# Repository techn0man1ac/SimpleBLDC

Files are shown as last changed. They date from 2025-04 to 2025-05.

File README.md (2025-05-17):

# SimpleBLDC

This is simple Arduino based 650W BLDC motor(with Hall sensors) controller. Designed with [KiCAD](https://www.kicad.org/). This controller has version V0.1, which means it is still under development. **The source files can be changed.**

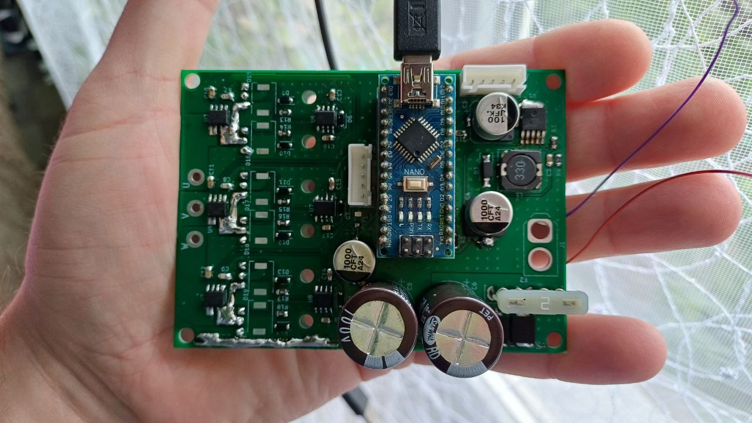
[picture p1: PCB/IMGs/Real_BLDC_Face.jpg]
SimpleBLDC PCB in real life


Simple BLDC 3-Phase BLDC motor driver specs:
- Battery: 8S 
- VCC: 24.0V to 33.6V
- I(max): 20A 
- Сurrent measurements per phase

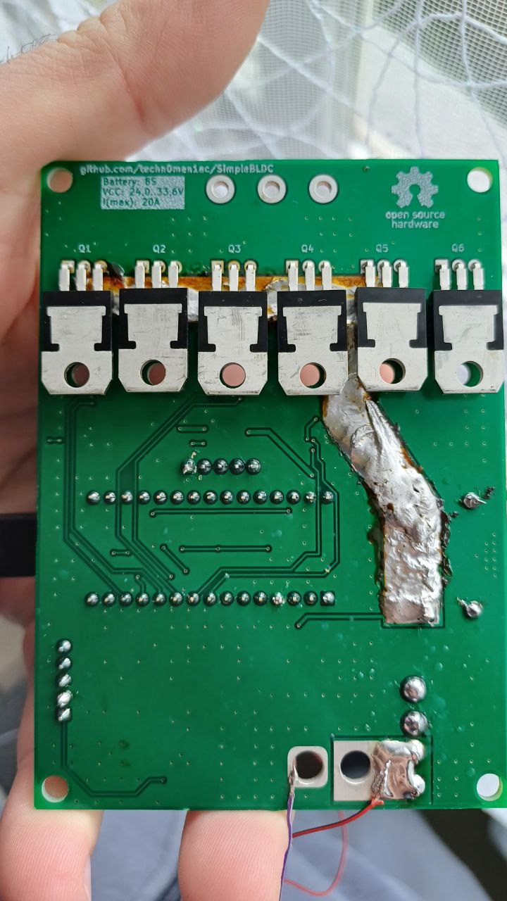
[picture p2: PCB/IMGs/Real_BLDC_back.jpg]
SimpleBLDC PCB in real life_back


The device has the following features:
- XT60 power connector;
- Arduino Nano V3.0 main controller;
- Overcurrent protection (fuse);
- Reverse polarity protection;
- The ability to work with non-collector motors via Hall sensors (electric scooter or electric bicycle);
- Monitoring and control of the current of each phase (current is measured in both positive and negative directions);
- Current control by PWM, operating frequency 16/32 kHz;
- Has a connector for connecting a traction control potentiometer and a reverse button.
- Publication of the project under the [MIT license](https://github.com/techn0man1ac/SimpleBLDC/blob/main/LICENSE).

# Schematic

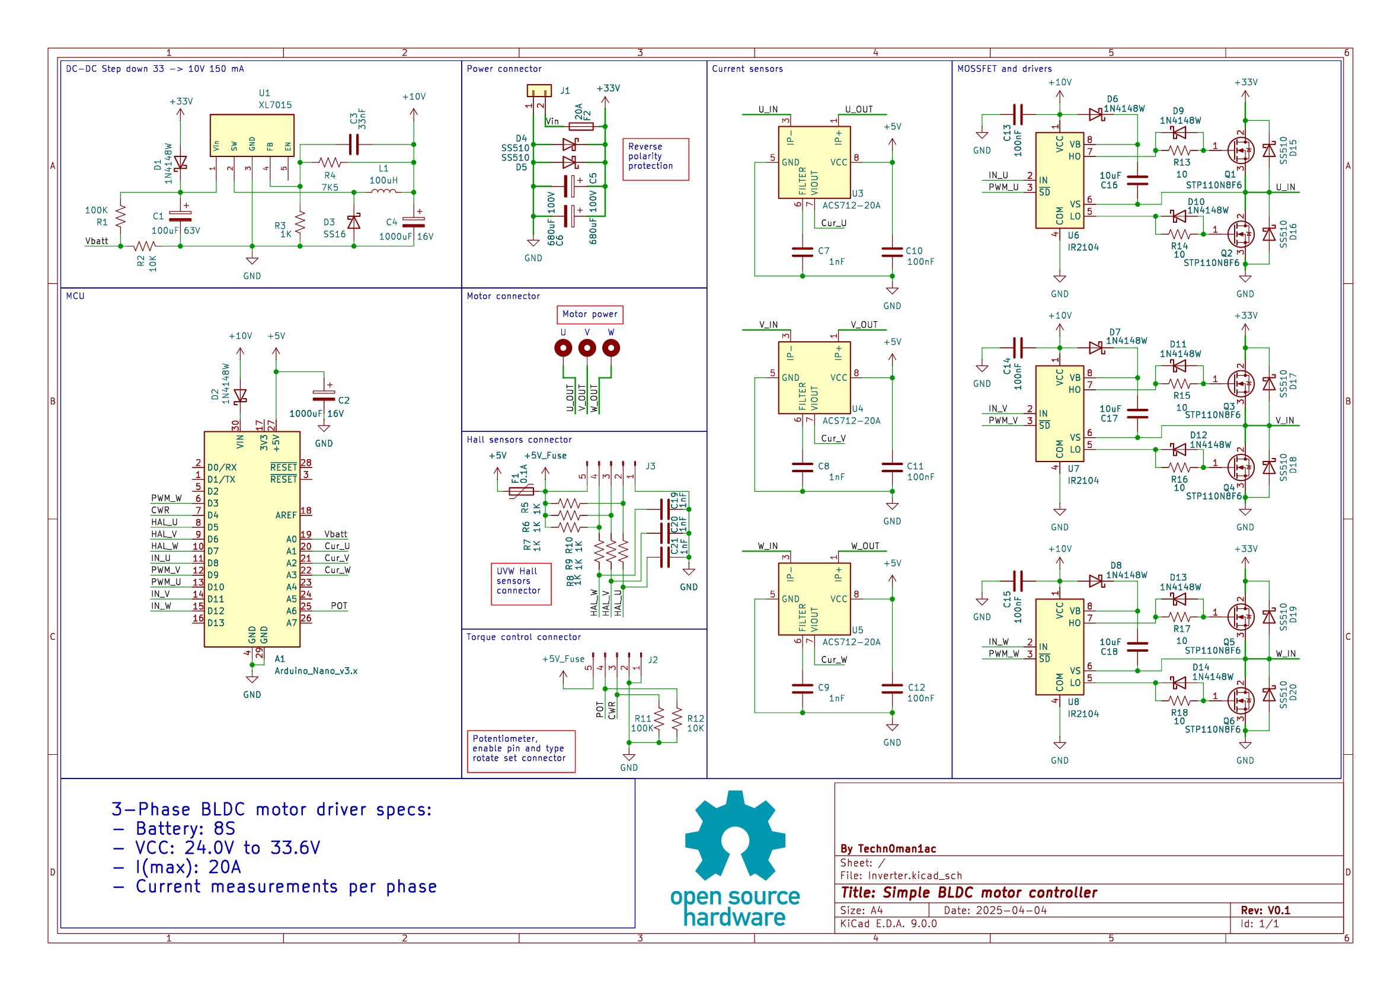
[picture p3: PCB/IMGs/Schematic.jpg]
BLDC motor driver schematic


The device has 3 drivers for mosfet transistors, as well as 3 current sensors based on the Hall effect, which measure both in the positive and negative directions. The use of 3 sensors is the reason for the development of the device for regenerative braking.

# PCB

The board consists of two layers: top and bottom. All the main parts are located on the top layer.

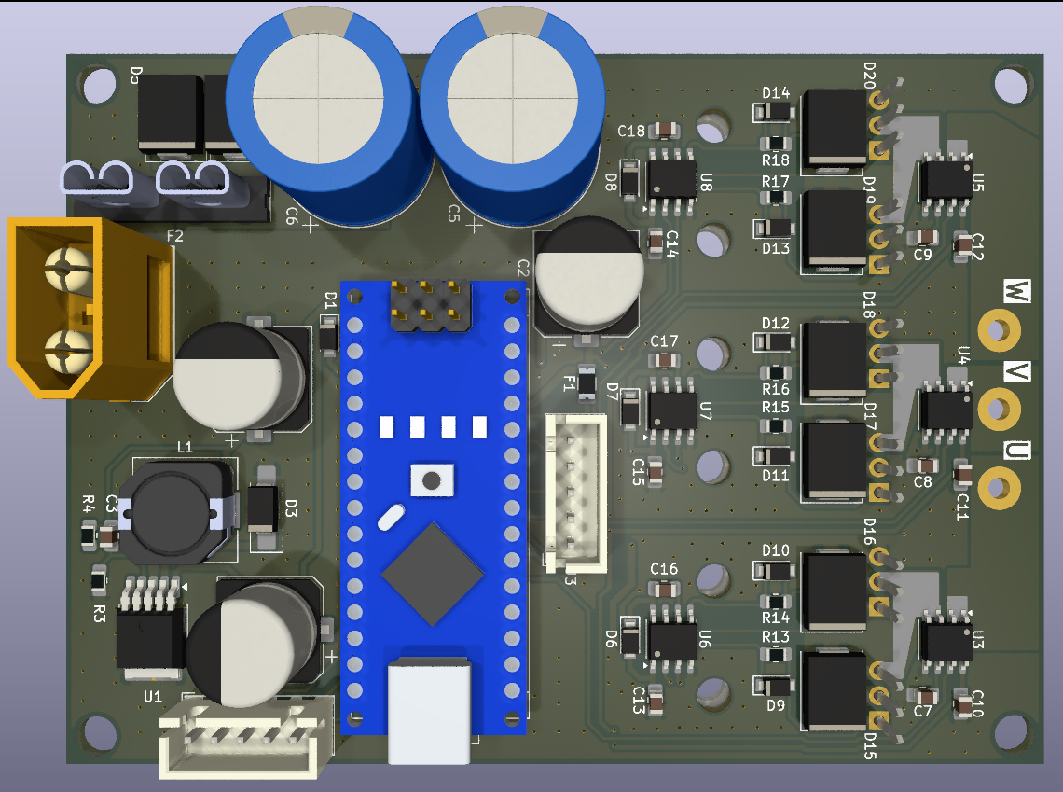
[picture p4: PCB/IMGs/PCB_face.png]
Face PCB side


The bottom layer contains mainly earth and power tracks.

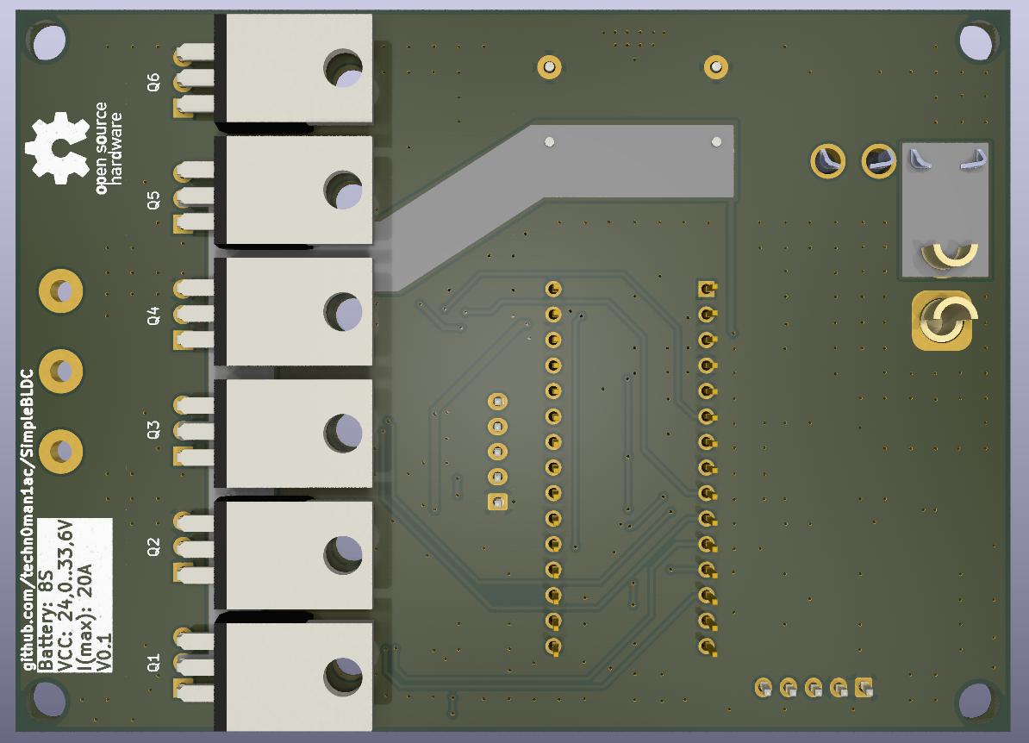
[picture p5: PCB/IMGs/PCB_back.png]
The PCB bottom laye


Board sizes is 72 x 99 mm:

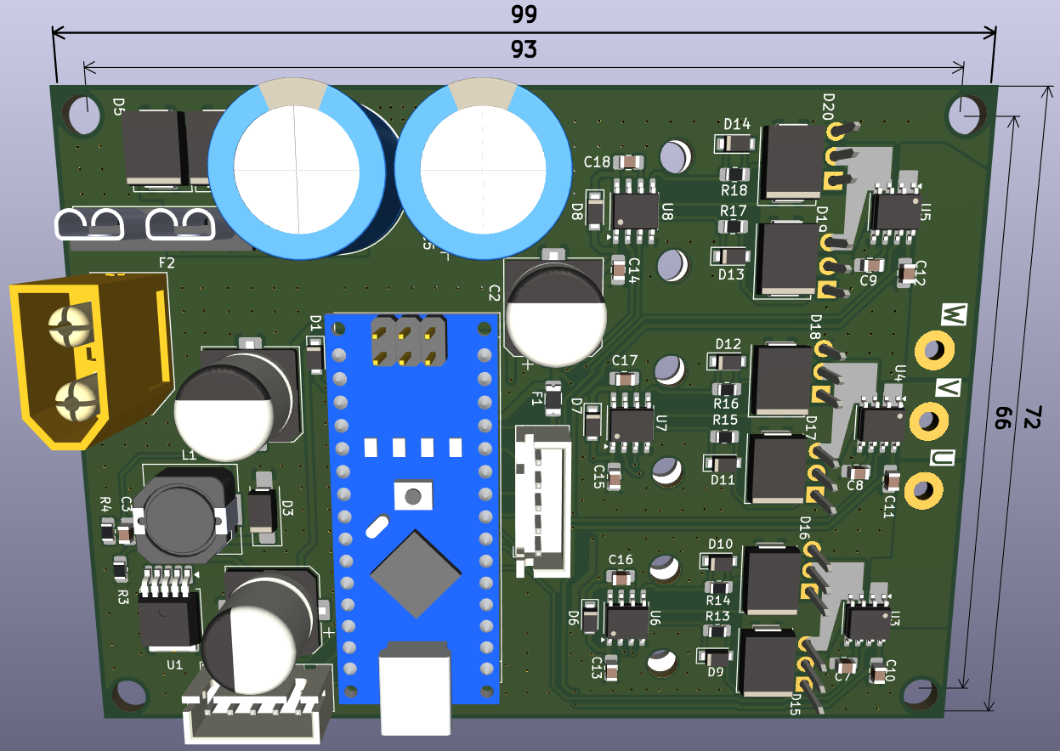
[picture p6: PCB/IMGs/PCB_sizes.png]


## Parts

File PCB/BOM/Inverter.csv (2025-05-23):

Reference | Qty | Value | DNP | Exclude from BOM | Exclude from Board | Footprint | Datasheet | Опис
A1 | 1 | Arduino_Nano_v3.x |  | Excluded from BOM |  | Module:Arduino_Nano | http://www.mouser.com/pdfdocs/Gravitech_Arduino_Nano3_0.pdf | Arduino Nano v3.x
C1 | 1 | 100uF 63V |  |  |  | Capacitor_SMD:CP_Elec_10x10.5 | ~ | Polarized capacitor
C2,C4 | 2 | 1000uF 16V |  |  |  | Capacitor_SMD:CP_Elec_10x10.5 | ~ | Polarized capacitor
C3 | 1 | 33nF |  |  |  | Capacitor_SMD:C_0805_2012Metric_Pad1.18x1.45mm_HandSolder | ~ | Unpolarized capacitor
C5,C6 | 2 | 680uF 100V |  |  |  | Capacitor_THT:CP_Radial_D16.0mm_P7.50mm | ~ | 680uF 100V 105C
C7,C8,C9,C19,C20,C21 | 6 | 1nF |  |  |  | Capacitor_SMD:C_0805_2012Metric_Pad1.18x1.45mm_HandSolder | ~ | Unpolarized capacitor
C10,C11,C12,C13,C14,C15 | 6 | 100nF |  |  |  | Capacitor_SMD:C_0805_2012Metric_Pad1.18x1.45mm_HandSolder | ~ | Unpolarized capacitor
C16,C17,C18 | 3 | 10uF |  |  |  | Capacitor_SMD:C_0805_2012Metric_Pad1.18x1.45mm_HandSolder | ~ | Unpolarized capacitor
D1,D2,D6,D7,D8,D9,D10,D11,D12,D13,D14 | 11 | 1N4148W |  |  |  | Diode_SMD:Nexperia_CFP3_SOD-123W | https://www.vishay.com/docs/86356/1n4148w.pdf | 100V 150mA 4ns 150mA SOD-123 Switching Diode
D3 | 1 | SS16 |  |  |  | Diode_SMD:D_SMA_Handsoldering | https://www.vishay.com/docs/88746/ss12.pdf | 60V 1A Schottky Diode, SMA
D4,D5,D15,D16,D17,D18,D19,D20 | 8 | SS510 |  |  |  | Diode_SMD:ST_D_SMC | https://www.rectron.com/public/product_datasheets/ss510.pdf | Schottky diode SS510 5A 100V SMC
F1 | 1 | 0.1A |  |  |  | Fuse:Fuse_1206_3216Metric | ~ | 16V 500mA 1206 Resettable Fuse
F2 | 1 | 20A |  |  |  | Fuse:FUSE_3522-2 | ~ | ATO Blade Fuse Holder
J1 | 1 | Conn_01x02 |  |  |  | Connector_AMASS:AMASS_XT60-M_1x02_P7.20mm_Vertical | ~ | Generic connector, single row, 01x02, script generated (kicad-library-utils/schlib/autogen/connector/)
J2,J3 | 2 | Conn_01x05_Pin |  |  |  | Connector_JST:JST_XH_B5B-XH-A_1x05_P2.50mm_Vertical | ~ | Generic connector, single row, 01x05, script generated
L1 | 1 | 100uH |  |  |  | Inductor_SMD:L_10.4x10.4_H4.8 | ~ | Inductor
Q1,Q2,Q3,Q4,Q5,Q6 | 6 | STP110N8F6 |  |  |  | Package_TO_SOT_THT:TO-220-3_Horizontal_TabUp | https://www.st.com/resource/en/datasheet/stp110n8f6.pdf | N-channel 80 V, 0.0056 Ω typ.,110 A, STripFET™ F6 Power MOSFET in a TO-220 package
R1,R11 | 2 | 100K |  |  |  | Resistor_SMD:R_0805_2012Metric_Pad1.20x1.40mm_HandSolder | ~ | Resistor, US symbol
R2,R12 | 2 | 10K |  |  |  | Resistor_SMD:R_0805_2012Metric_Pad1.20x1.40mm_HandSolder | ~ | Resistor, US symbol
R3,R5,R6,R7,R8,R9,R10 | 7 | 1K |  |  |  | Resistor_SMD:R_0805_2012Metric_Pad1.20x1.40mm_HandSolder | ~ | Resistor, US symbol
R4 | 1 | 7K5 |  |  |  | Resistor_SMD:R_0805_2012Metric_Pad1.20x1.40mm_HandSolder | ~ | Resistor, US symbol
R13,R14,R15,R16,R17,R18 | 6 | 10 |  |  |  | Resistor_SMD:R_0805_2012Metric_Pad1.20x1.40mm_HandSolder | ~ | Resistor, US symbol
U1 | 1 | XL7015 |  |  |  | Package_TO_SOT_SMD:TO-252-5_TabPin3 | kicad-embed://datasheet-xl7015.pdf | Step-down type Adjustable 0.8A 5V~80V TO-252-5 DC-DC Converter
U2,V1,W1 | 3 | MountingHole_Pad |  | Excluded from BOM |  | MountingHole:MountingHole_2.2mm_M2_Pad | ~ | Mounting Hole with connection
U3,U4,U5 | 3 | ACS712-20A |  |  |  | Package_SO:SOIC-8_3.9x4.9mm_P1.27mm | http://www.allegromicro.com/~/media/Files/Datasheets/ACS712-Datasheet.ashx?la=en | ±20A Bidirectional Hall-Effect Current Sensor, +5.0V supply, 100mV/A, SOIC-8
U6,U7,U8 | 3 | IR2104 |  |  |  | Package_SO:SOIC-8_3.9x4.9mm_P1.27mm | https://www.infineon.com/dgdl/ir2104.pdf?fileId=5546d462533600a4015355c7c1c31671 | Half-Bridge Driver, 600V, 210/360mA, PDIP-8/SOIC-8

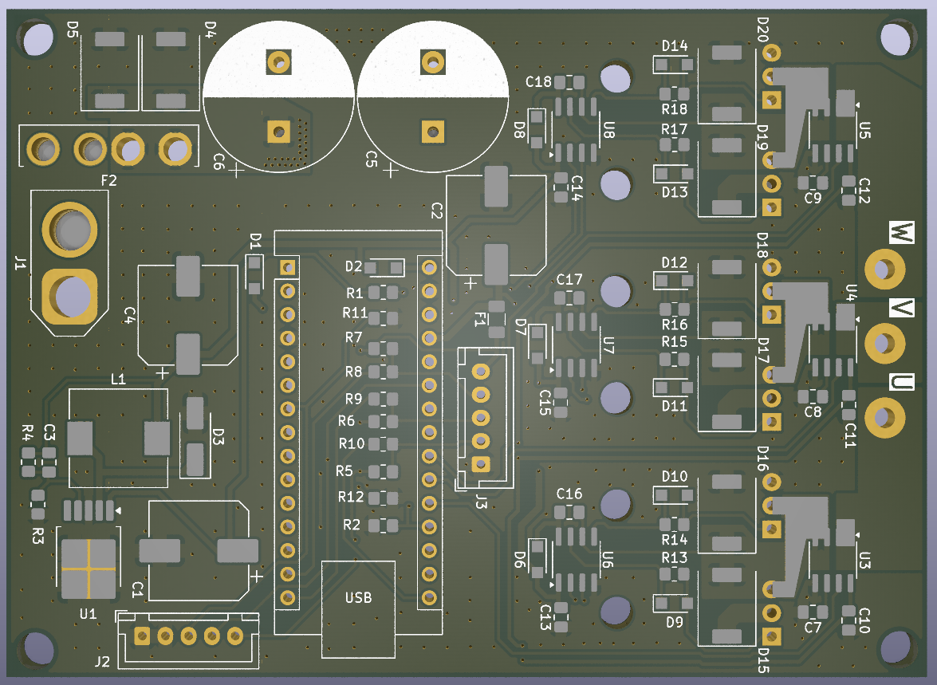
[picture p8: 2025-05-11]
PCB/IMGs/PCB_face_without_components.png

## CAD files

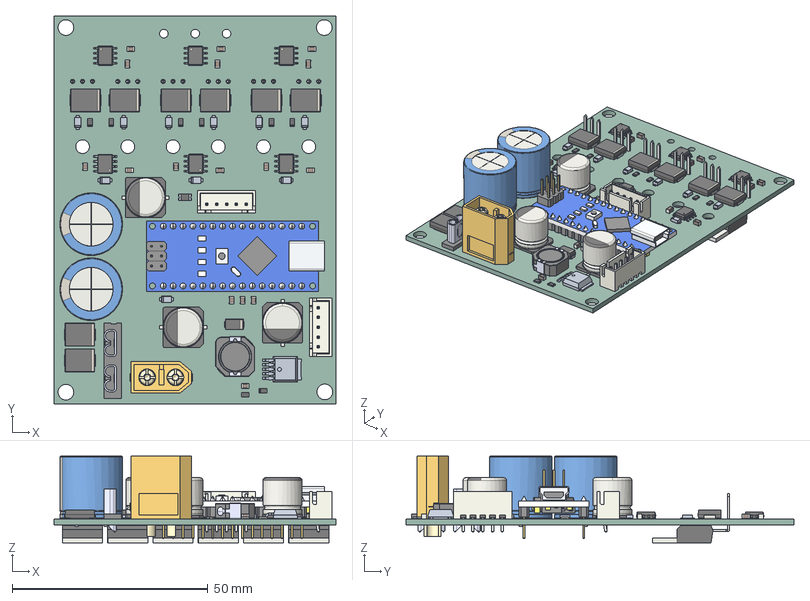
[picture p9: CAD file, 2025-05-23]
PCB/Board3D/Inverter.step
71.9 x 99.1 x 22.1 mm
JST_XH_B5B-XH-A_1x05_P2.50mm_Vertical x 2
D_SMC x 8
C_0805_2012Metric x 16
Inverter 1.5.1 x 11
R_0805_2012Metric x 18
SOIC-8_3.9x4.9mm_P1.27mm x 6
CP_Radial_D16.0mm_P7.50mm x 2
CDRH104RNP-150NC
CP_Elec_10x10.5 x 3
Arduino_Nano
Inverter 1.36.1
D_SMA
AMASS_XT60-M_1x02_P7.2mm_Vertical
solidIntersect
Terminal
TO-220-3_Horizontal_TabUp x 6
Inverter_PCB

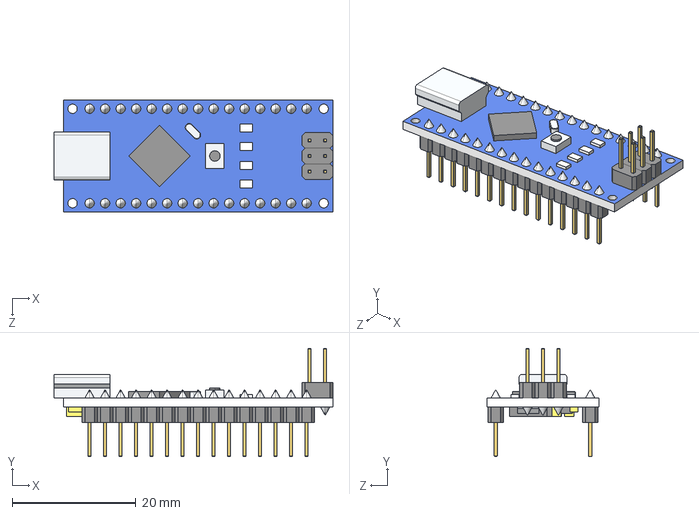
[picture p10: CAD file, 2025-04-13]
PCB/Components/Arduino/Arduino_Nano.STEP
45.0 x 17.5 x 18.0 mm

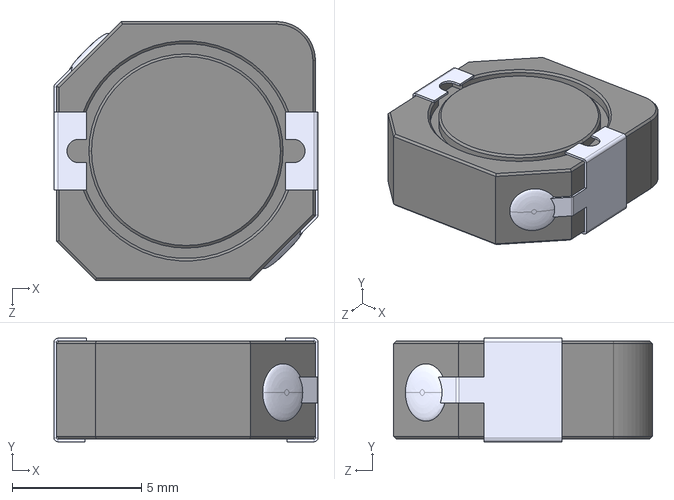
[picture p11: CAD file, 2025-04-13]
PCB/Components/CDRH104RNP/CDRH104RNP-150NC.STEP
10.2 x 4.00 x 10.0 mm

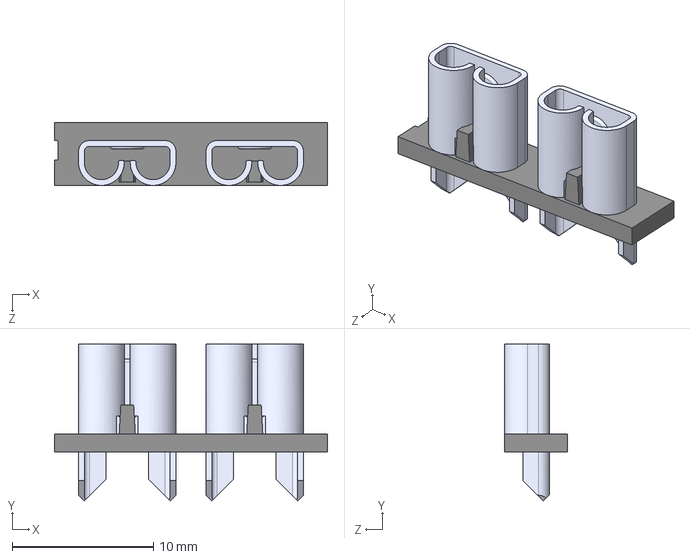
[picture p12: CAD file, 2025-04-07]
PCB/Components/Fuse Clips/3522-2--3DModel-STEP-56544.STEP
19.3 x 11.1 x 4.45 mm

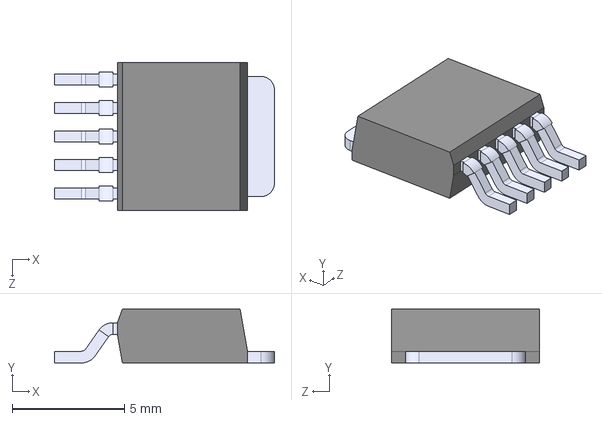
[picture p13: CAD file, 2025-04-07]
PCB/Components/XL7015/XL7015--3DModel-STEP-510211.STEP
9.80 x 2.40 x 6.60 mm

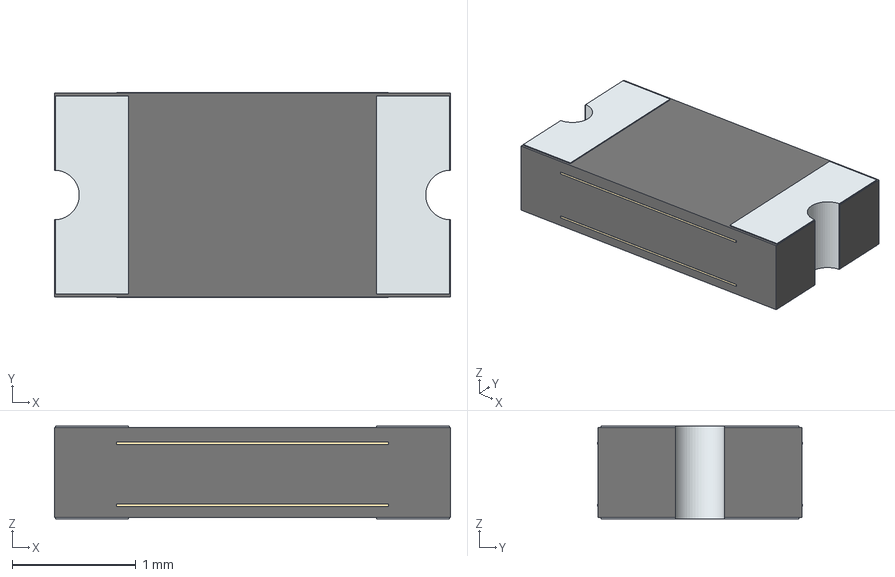
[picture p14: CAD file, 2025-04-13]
PCB/Components/PolyFuse/1206L035YR.stp
3.20 x 1.65 x 0.75 mm
solidIntersect
Terminal

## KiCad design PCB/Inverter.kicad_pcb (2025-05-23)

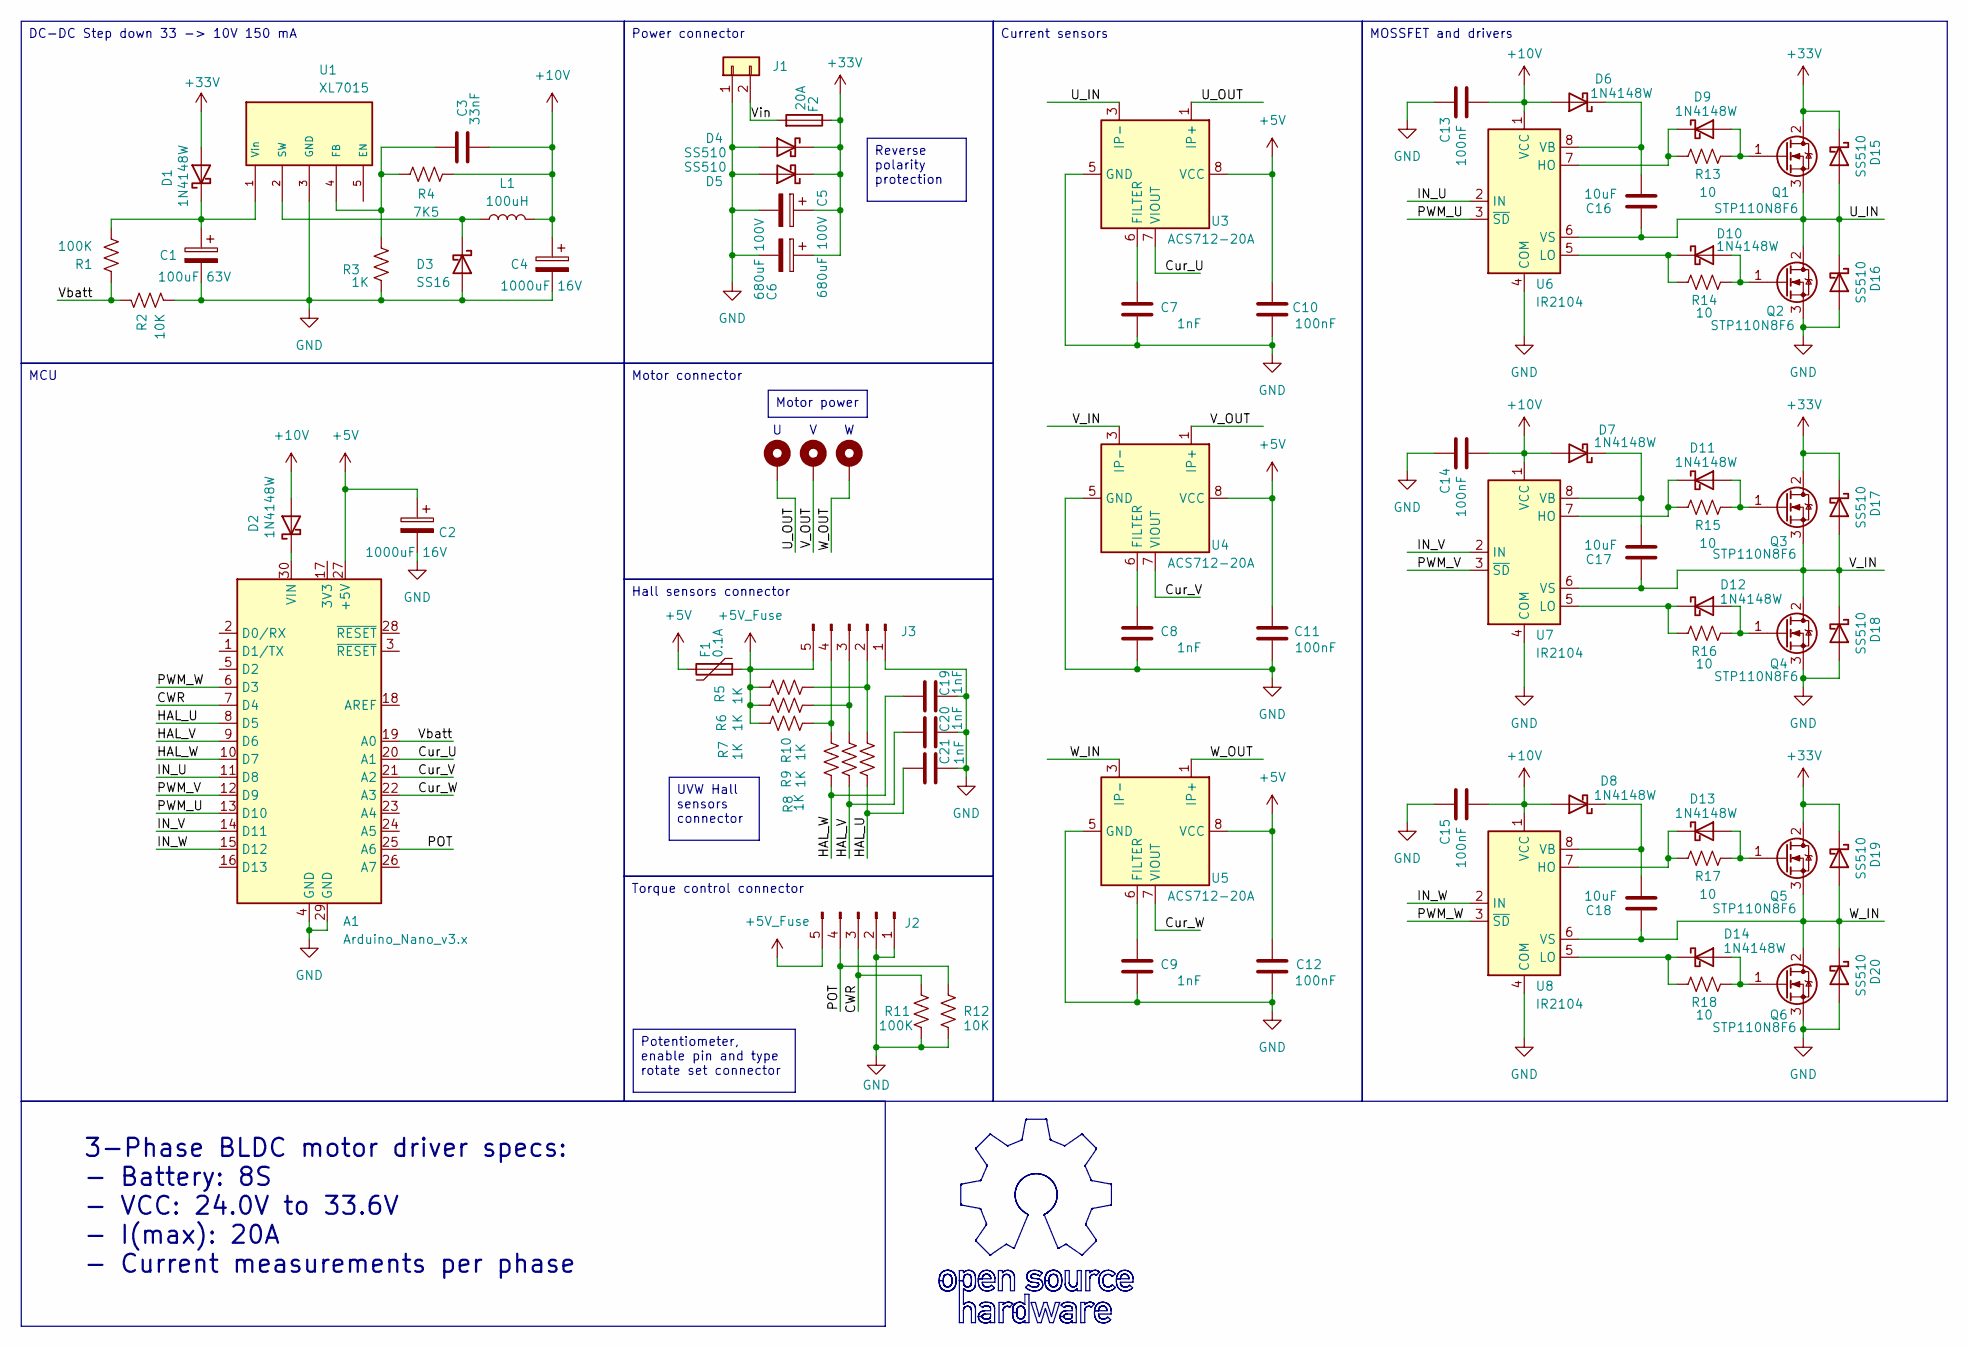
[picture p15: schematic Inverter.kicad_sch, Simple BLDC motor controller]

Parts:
A1: Arduino_Nano_v3.x; Arduino_Nano
C1: 100uF 63V; CP_Elec_10x10.5
C2, C4: 1000uF 16V; CP_Elec_10x10.5
C3: 33nF; C_0805_2012Metric_Pad1.18x1.45mm_HandSolder
C5, C6: 680uF 100V; CP_Radial_D16.0mm_P7.50mm
C7, C8, C9, C19, C20, C21: 1nF; C_0805_2012Metric_Pad1.18x1.45mm_HandSolder
C10, C11, C12, C13, C14, C15: 100nF; C_0805_2012Metric_Pad1.18x1.45mm_HandSolder
C16, C17, C18: 10uF; C_0805_2012Metric_Pad1.18x1.45mm_HandSolder
D1, D2, D6, D7, D8, D9, D10, D11, D12, D13, D14: 1N4148W; Nexperia_CFP3_SOD-123W
D3: SS16; D_SMA_Handsoldering
D4, D5, D15, D16, D17, D18, D19, D20: SS510; ST_D_SMC
F1: 0.1A; Fuse_1206_3216Metric
F2: 20A; FUSE_3522-2
J1: Conn_01x02; AMASS_XT60-M_1x02_P7.20mm_Vertical
J2, J3: Conn_01x05_Pin; JST_XH_B5B-XH-A_1x05_P2.50mm_Vertical
L1: 100uH; L_10.4x10.4_H4.8
Q1, Q2, Q3, Q4, Q5, Q6: STP110N8F6; TO-220-3_Horizontal_TabUp
R1, R11: 100K; R_0805_2012Metric_Pad1.20x1.40mm_HandSolder
R2, R12: 10K; R_0805_2012Metric_Pad1.20x1.40mm_HandSolder
R3, R5, R6, R7, R8, R9, R10: 1K; R_0805_2012Metric_Pad1.20x1.40mm_HandSolder
R4: 7K5; R_0805_2012Metric_Pad1.20x1.40mm_HandSolder
R13, R14, R15, R16, R17, R18: 10; R_0805_2012Metric_Pad1.20x1.40mm_HandSolder
U1: XL7015; TO-252-5_TabPin3
U2: MountingHole_Pad; MountingHole_2.2mm_M2_Pad
U3, U4, U5: ACS712-20A; SOIC-8_3.9x4.9mm_P1.27mm
U6, U7, U8: IR2104; SOIC-8_3.9x4.9mm_P1.27mm
V1: MountingHole_Pad; MountingHole_2.2mm_M2_Pad
W1: MountingHole_Pad; MountingHole_2.2mm_M2_Pad

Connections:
+5V: A1.27 (+5V), C2.1, C10.1, C11.1, C12.1, F1.2, U3.8 (VCC), U4.8 (VCC), U5.8 (VCC)
+5V_Fuse: F1.1, J2.5, J3.5, R5.2, R6.2, R7.2
+10V: C3.2, C4.1, C13.2, C14.2, C15.2, D2.2 (A), D6.2 (A), D7.2 (A), D8.2 (A), L1.2, R4.1, U6.1 (VCC), U7.1 (VCC), U8.1 (VCC)
+33V: C5.1, C6.1, D1.2 (A), D4.1 (K), D5.1 (K), D15.1 (K), D17.1 (K), D19.1 (K), F2.1, Q1.2 (D), Q3.2 (D), Q5.2 (D)
/CWR: A1.7 (D4), J2.3, R11.2
/Cur_U: A1.20 (A1), U3.7 (VIOUT)
/Cur_V: A1.21 (A2), U4.7 (VIOUT)
/Cur_W: A1.22 (A3), U5.7 (VIOUT)
/HAL_U: A1.8 (D5), C21.1, R10.1
/HAL_V: A1.9 (D6), C20.1, R9.1
/HAL_W: A1.10 (D7), C19.1, R8.1
/IN_U: A1.11 (D8), U6.2 (IN)
/IN_V: A1.14 (D11), U7.2 (IN)
/IN_W: A1.15 (D12), U8.2 (IN)
/POT: A1.25 (A6), J2.4, R12.2
/PWM_U: A1.13 (D10), U6.3 (~SD)
/PWM_V: A1.12 (D9), U7.3 (~SD)
/PWM_W: A1.6 (D3), U8.3 (~SD)
/U_IN: C16.1, D15.2 (A), D16.1 (K), Q1.3 (S), Q2.2 (D), U3.3 (IP-), U3.4 (IP-), U6.6 (VS)
/U_OUT: U2.1, U3.1 (IP+), U3.2 (IP+)
/V_IN: C17.1, D17.2 (A), D18.1 (K), Q3.3 (S), Q4.2 (D), U4.3 (IP-), U4.4 (IP-), U7.6 (VS)
/V_OUT: U4.1 (IP+), U4.2 (IP+), V1.1
/Vbatt: A1.19 (A0), R1.2, R2.2
/Vin: F2.2, J1.2
/W_IN: C18.1, D19.2 (A), D20.1 (K), Q5.3 (S), Q6.2 (D), U5.3 (IP-), U5.4 (IP-), U8.6 (VS)
/W_OUT: U5.1 (IP+), U5.2 (IP+), W1.1
GND: A1.4 (GND), A1.29 (GND), C1.2, C2.2, C4.2, C5.2, C6.2, C7.2, C8.2, C9.2, C10.2, C11.2, C12.2, C13.1, C14.1, C15.1, C19.2, C20.2, C21.2, D3.2 (A), D4.2 (A), D5.2 (A), D16.2 (A), D18.2 (A), D20.2 (A), J1.1, J2.1, J2.2, J3.1, Q2.3 (S), Q4.3 (S), Q6.3 (S), R2.1, R3.1, R11.1, R12.1, U1.3 (GND), U3.5 (GND), U4.5 (GND), U5.5 (GND), U6.4 (COM), U7.4 (COM), U8.4 (COM)
unnamed: A1.30 (VIN), D2.1 (K)
unnamed: C1.1, D1.1 (K), R1.1, U1.1 (Vin)
unnamed: D3.1 (K), L1.1, U1.2 (SW)
unnamed: C16.2, D6.1 (K), U6.8 (VB)
unnamed: C17.2, D7.1 (K), U7.8 (VB)
unnamed: C18.2, D8.1 (K), U8.8 (VB)
unnamed: D9.2 (A), Q1.1 (G), R13.1
unnamed: D9.1 (K), R13.2, U6.7 (HO)
unnamed: D10.2 (A), Q2.1 (G), R14.1
unnamed: D10.1 (K), R14.2, U6.5 (LO)
unnamed: D11.2 (A), Q3.1 (G), R15.1
unnamed: D11.1 (K), R15.2, U7.7 (HO)
unnamed: D12.2 (A), Q4.1 (G), R16.1
unnamed: D12.1 (K), R16.2, U7.5 (LO)
unnamed: D13.2 (A), Q5.1 (G), R17.1
unnamed: D13.1 (K), R17.2, U8.7 (HO)
unnamed: D14.2 (A), Q6.1 (G), R18.1
unnamed: D14.1 (K), R18.2, U8.5 (LO)
unnamed: J3.2, R5.1, R10.2
unnamed: J3.3, R6.1, R9.2
unnamed: J3.4, R7.1, R8.2
unnamed: C3.1, R3.2, R4.2, U1.4 (FB)
unnamed: C7.1, U3.6 (FILTER)
unnamed: C8.1, U4.6 (FILTER)
unnamed: C9.1, U5.6 (FILTER)

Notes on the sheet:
Power connector
3-Phase BLDC motor driver specs: - Battery: 8S - VCC: 24.0V to 33.6V - I(max): 20A - Сurrent measurements per phase
Reverse polarity protection
Current sensors
MOSSFET and drivers
Motor connector
UVW Hall sensors connector
Hall sensors connector
Motor power
MCU
DC-DC Step down 33 -> 10V 150 mA
Torque control connector
Potentiometer, enable pin and type rotate set connector

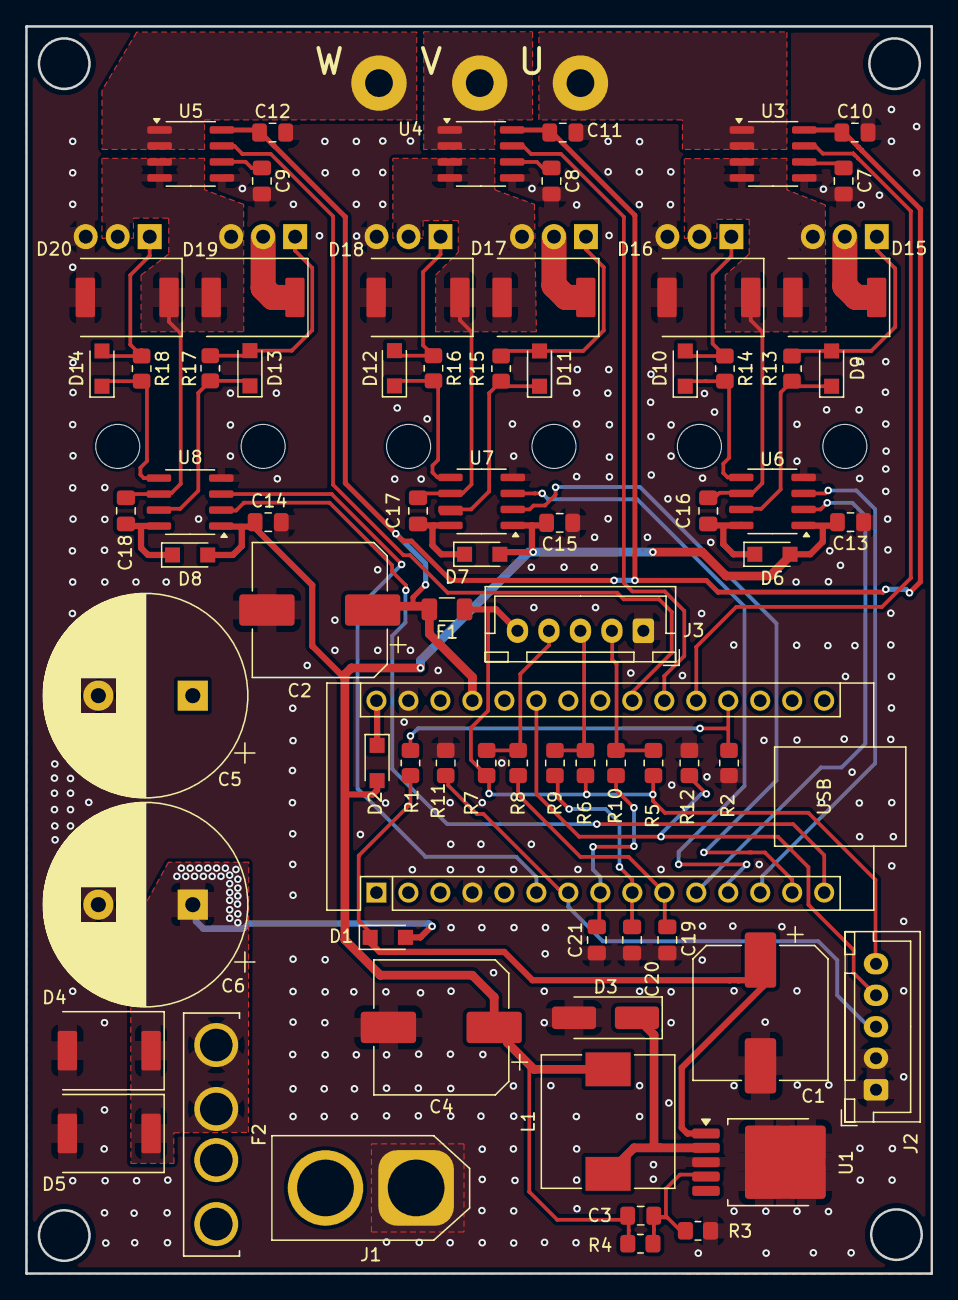
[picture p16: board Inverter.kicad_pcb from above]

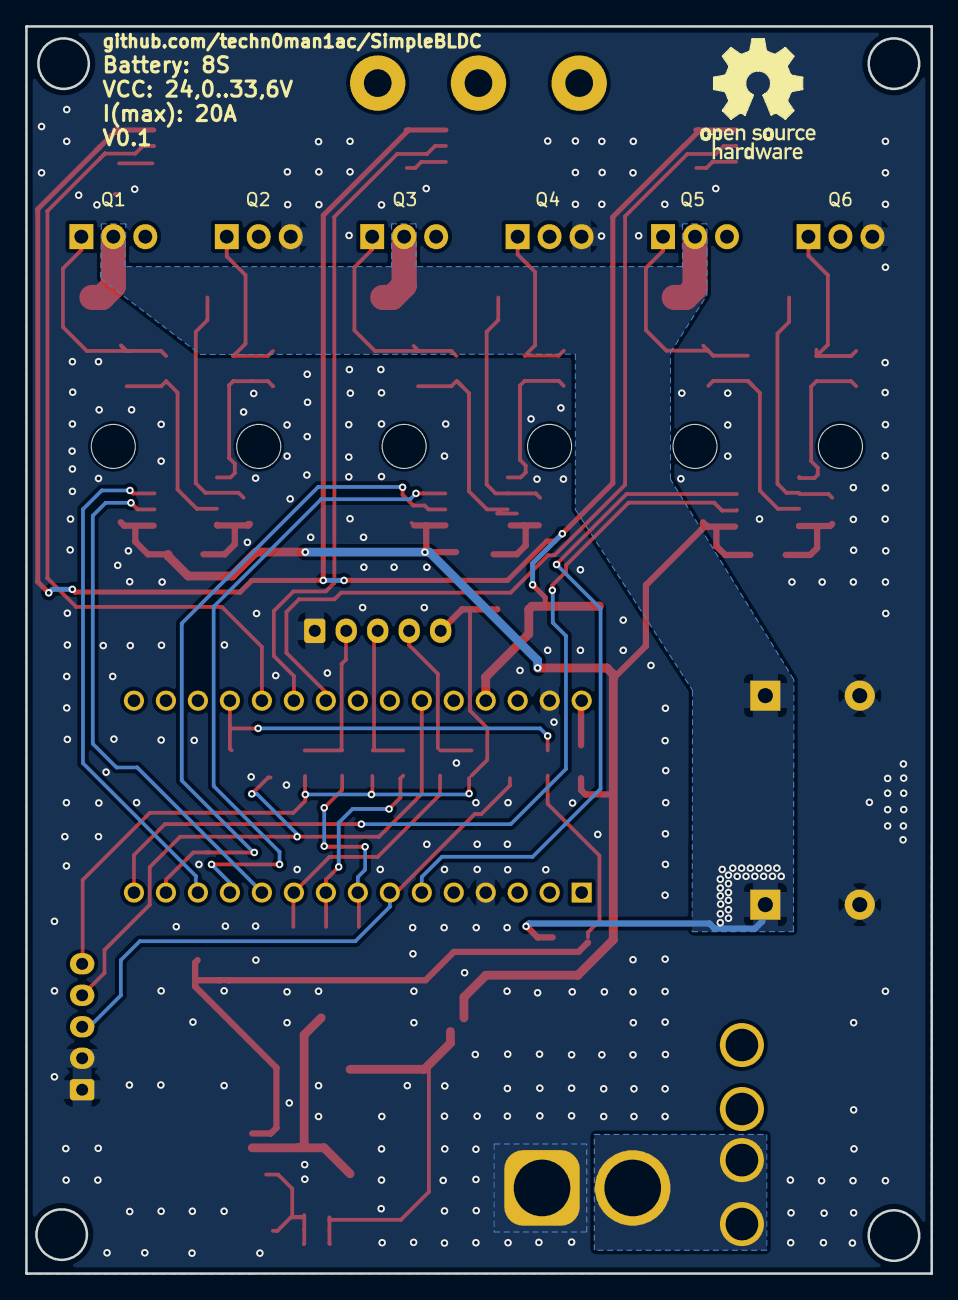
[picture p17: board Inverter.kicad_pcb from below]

Board: 2 copper layers, 71.9 x 99.1 mm, 82 parts (6 on the bottom side), 52 nets.

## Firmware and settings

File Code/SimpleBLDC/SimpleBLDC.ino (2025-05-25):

/*

    This is simple Arduino based 650W BLDC motor(with Hall sensors) controller.
    https://github.com/techn0man1ac/SimpleBLDC

*/

#define SET_PWM_16Khz true // Set PWM transistors frequency 16 kHz

#if SET_PWM_16Khz == true
#include <avr/power.h>
#define F_CPU 800000UL  // CPU frequency set to 8 MHz mode
#endif

#define PWM_U 10
#define PWM_V 9
#define PWM_W 3
#define IN_U 8
#define IN_V 11
#define IN_W 12
#define HAL_U 5
#define HAL_V 6
#define HAL_W 7
#define Vbatt A0
#define Cur_U A1
#define Cur_V A2
#define Cur_W A3
#define POT A6
#define CWR 4

volatile byte Hall_State = 0;

float BattVoltage = 0.0;
int VoltageRAW = 0;

int U_CurrentRAW = 0;
int V_CurrentRAW = 0;
int W_CurrentRAW = 0;

float U_Current = 0.0;
float V_Current = 0.0;
float W_Current = 0.0;

float Voltage_Coef = (55.0 / 1023.0);
float U_Current_Coef = (5.0 / 511.0);
float V_Current_Coef = (5.0 / 511.0);
float W_Current_Coef = (5.0 / 511.0);

int PWM = 165; // Current limit

unsigned long previousMillis = 0;
int interval = 100; // Telemetry interval

void setup() {
  Serial.begin(115200);

#if SET_PWM_16Khz == true
  clock_prescale_set(clock_div_2); // Set CPU to 8 MHz mode
  Serial.begin(230400); // Mean 115200(becouse CPU frequency down 2)
  interval = interval / 2;
#endif

  pinMode(PWM_U, OUTPUT);
  pinMode(PWM_V, OUTPUT);
  pinMode(PWM_W, OUTPUT);
  pinMode(IN_U, OUTPUT);
  pinMode(IN_V, OUTPUT);
  pinMode(IN_W, OUTPUT);
  pinMode(HAL_U, INPUT);
  pinMode(HAL_V, INPUT);
  pinMode(HAL_W, INPUT);

  setPWMPrescaler(PWM_U, 1);
  setPWMPrescaler(PWM_V, 1);
  setPWMPrescaler(PWM_W, 1);

  // Using Arduino Interrupts https://dronebotworkshop.com/interrupts/
  // Enable PCIE2 Bit2 = 1 (Port D)
  PCICR |= B00000100;
  // Select PCINT21, PCINT22, PCINT23 = 1 (Pin D5, D6, D7)
  PCMSK2 |= B11100000;

  MotorRun(0); // Inintalization
  delay(1000);
  Hall_State = HallSensorsRead();
  MotorRun(Hall_State);
}

void loop() {
  U_CurrentRAW = analogRead(Cur_U);
  V_CurrentRAW = analogRead(Cur_V);
  W_CurrentRAW = analogRead(Cur_W);

  VoltageRAW = analogRead(Vbatt);

  BattVoltage = VoltageRAW * Voltage_Coef;

  U_Current = (U_CurrentRAW - 518) * U_Current_Coef;
  V_Current = (V_CurrentRAW - 518) * V_Current_Coef;
  W_Current = (W_CurrentRAW - 516) * W_Current_Coef;

  unsigned long currentMillis = millis();

  if (currentMillis - previousMillis >= interval) {
    previousMillis = currentMillis;

    Serial.println(String(U_Current) + "," + String(V_Current) + "," + String(W_Current) + "," + String(Hall_State) + "," + String(BattVoltage));
  }
}

ISR (PCINT2_vect) {
  Hall_State = HallSensorsRead();
  MotorRun(Hall_State);
}

int HallSensorsRead() {
  return PIND >> 5;
}

// Six-Step (Trapezoidal) Commutation https://onlinedocs.microchip.com/oxy/GUID-ED5A4EC0-70D9-40E8-82A4-9EE711C91C4E-en-US-11/GUID-A2E50F02-E898-425F-B2A2-36E161DE810B.html
void MotorRun(int SensorState) {
  switch (SensorState) {
    case 1: // 100 Step 4
      analogWrite(PWM_U, PWM); digitalWrite(IN_U, LOW);
      analogWrite(PWM_V, PWM); digitalWrite(IN_V, HIGH);
      analogWrite(PWM_W, 0);   digitalWrite(IN_W, LOW);
      break;

    case 2: // 010 Step 6
      analogWrite(PWM_U, 0);   digitalWrite(IN_U, LOW);
      analogWrite(PWM_V, PWM); digitalWrite(IN_V, LOW);
      analogWrite(PWM_W, PWM); digitalWrite(IN_W, HIGH);
      break;

    case 3: // 110 Step 5
      analogWrite(PWM_U, PWM); digitalWrite(IN_U, LOW);
      analogWrite(PWM_V, 0);   digitalWrite(IN_V, LOW);
      analogWrite(PWM_W, PWM); digitalWrite(IN_W, HIGH);
      break;

    case 4: // 001 Step 2
      analogWrite(PWM_U, PWM); digitalWrite(IN_U, HIGH);
      analogWrite(PWM_V, 0);   digitalWrite(IN_V, LOW);
      analogWrite(PWM_W, PWM); digitalWrite(IN_W, LOW);
      break;

    case 5: // 101 Step 3
      analogWrite(PWM_U, 0);   digitalWrite(IN_U, LOW);
      analogWrite(PWM_V, PWM); digitalWrite(IN_V, HIGH);
      analogWrite(PWM_W, PWM); digitalWrite(IN_W, LOW);
      break;

    case 6: // 011 Step 1
      analogWrite(PWM_U, PWM); digitalWrite(IN_U, HIGH);
      analogWrite(PWM_V, PWM); digitalWrite(IN_V, LOW);
      analogWrite(PWM_W, 0);   digitalWrite(IN_W, LOW);

      break;

    default:
      // turn off all transistors and read hall sensors:
      analogWrite(PWM_U, 0); digitalWrite(IN_U, LOW);
      analogWrite(PWM_V, 0); digitalWrite(IN_V, LOW);
      analogWrite(PWM_W, 0); digitalWrite(IN_W, LOW);
      // Read Hall sensors
      Hall_State = HallSensorsRead();
  }
}

// How to change the PWM frequency on Arduino https://www.luisllamas.es/en/change-pwm-frequency-arduino/
void setPWMPrescaler(uint8_t pin, uint16_t prescale) {

  byte mode;

  if (pin == 5 || pin == 6 || pin == 9 || pin == 10) {
    switch (prescale) {
      case    1: mode = 0b001; break;
      case    8: mode = 0b010; break;
      case   64: mode = 0b011; break;
      case  256: mode = 0b100; break;
      case 1024: mode = 0b101; break;
      default: return;
    }

  } else if (pin == 3 || pin == 11) {
    switch (prescale) {
      case    1: mode = 0b001; break;
      case    8: mode = 0b010; break;
      case   32: mode = 0b011; break;
      case   64: mode = 0b100; break;
      case  128: mode = 0b101; break;
      case  256: mode = 0b110; break;
      case 1024: mode = 0b111; break;
      default: return;
    }
  }

  if (pin == 5 || pin == 6) {
    TCCR0B = TCCR0B & 0b11111000 | mode;
  } else if (pin == 9 || pin == 10) {
    TCCR1B = TCCR1B & 0b11111000 | mode;
  } else if (pin == 3 || pin == 11) {
    TCCR2B = TCCR2B & 0b11111000 | mode;
  }
}

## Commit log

2025-04-06 Change#000
    Start
    [Inverter.kicad_pcb, Inverter.kicad_sch]
2025-04-06 Change#000
    Start second try
    [Inverter.kicad_sch]
2025-04-07 Change#001
    I replaced the DC-DC converter chip with a higher voltage one, 80 V versus 40 V as before.
    [3522-2--3DModel-STEP-56544.STEP, 3522-2.step, Inverter.kicad_sch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]
2025-04-07 #Change002
    Add device parameters
    [Inverter.kicad_sch]
2025-04-07 Change#002
    Add specs and schematic image
2025-04-09 Change#003
    Schematic changes
    [Inverter.kicad_pcb, Inverter.kicad_sch]
2025-04-09 Change#004
    Update schematics
2025-04-13 Change#005
    PCB 90%
    [1206L035YR.stp, 3522-2--3DModel-STEP-56544.STEP, 3522-2.step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]
2025-04-13 Change#005
    Cosmetics
    [Inverter.kicad_sch]
2025-04-13 Change#006
    Add PCB gerber files.
    [1206L035YR.stp, 3522-2--3DModel-STEP-56544.STEP, 3522-2.step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]
2025-04-14 Change#007
    Add OSHW logo and PCB 3d model in step format
    [Inverter-B_Cu.gbr, Inverter-B_Mask.gbr, Inverter-B_Paste.gbr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]
2025-04-22 Change#008
    Ready for fabrication
    [1206L035YR.stp, 3522-2--3DModel-STEP-56544.STEP, 3522-2.step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]
2025-05-11 Change#009
    Changed the pin on phase W from 5 to 3 (so that all PWMs are at the same frequency);
    Added a thermal barrier for all components on the negative side to make it easier to assemble the device;
    Changed the size of the board, it became a little larger (to increase the ground current);
    Added frames for connectors with a description in the diagram for a better understanding of which connector is for what.
    [Inverter-B_Cu.gbr, Inverter-B_Mask.gbr, Inverter-B_Paste.gbr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]
2025-05-11 Change#009
    Actual gerbers files
2025-05-11 Change#009
    Add Arduino code
2025-05-11 Change#009
    Add photo real device.
2025-05-17 Change#011
    Change hall sensor pin 13 -> 5
    [1206L035YR.stp, 3522-2--3DModel-STEP-56544.STEP, 3522-2.step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]
2025-05-17 Change#011
    Add real device photos
2025-05-17 Change#012
    Work code
    https://www.youtube.com/shorts/_VDWO1sNHf8
    [SimpleBLDC.ino]
2025-05-17 Change#012
    Add new version of code, many fixes
    [SimpleBLDC.ino]
2025-05-19 Change#013
    Add interrupt for hall sensors
2025-05-22 Change#012
    The outputs on the board for setting the operation of half-bridges have been changed, as well as the inputs for Hall sensors, so that they are in the space of one port and read by one line of code, a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
    [Inverter-B_Cu.gbr, Inverter-B_Mask.gbr, Inverter-B_Paste.gbr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]
2025-05-22 Change#013
    Delete PCB/Gerbers/Gerbers.zip
2025-05-23 Change#014
    Added capacitors for the outputs from the Hall sensors.
    [Inverter-B_Cu.gbr, Inverter-B_Mask.gbr, Inverter-B_Paste.gbr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]
2025-05-23 Change#014
    Delete PCB/Gerbers/Inverter_Gerbers.zip
2025-05-23 Change#014
    Add 3 filtering capacitors
    [Inverter.csv]
2025-05-25 Change#015
    Add set PWM transistors frequency 16 kHz flag
2026-06-01 Change#016
    I have updated the source code, which uses the SimpleFOC library to implement many functions, such as precise positioning, motor speed control, motor parameter measurement, and implementation of the 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
